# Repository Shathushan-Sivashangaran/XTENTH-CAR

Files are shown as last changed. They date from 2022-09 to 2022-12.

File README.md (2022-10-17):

# XTENTH-CAR
XTENTH-CAR (eXperimental one-TENTH scaled vehicle platform for Connected autonomy and All-terrain Research) aims to increase accessibility of experimental Connected Autonomous Vehicle (CAV) and Autonomous Ground Vehicle (AGV) research with low upfront costs, and complete Autonomous Vehicle (AV) hardware and software architectures, similar to the full-sized X-CAR experimental vehicle platform, enabling efficient cross-platform development between small-scale and full-scale vehicles [1], [2].

<p align="center">
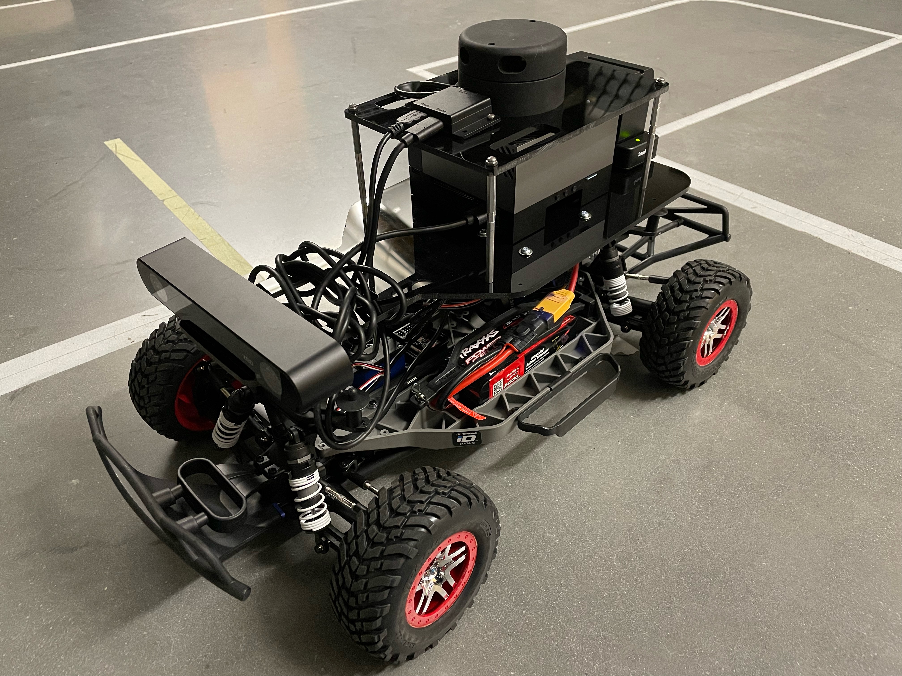
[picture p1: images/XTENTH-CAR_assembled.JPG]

</p>

## Hardware Build
The platform is equipped with the best-in-class NVIDIA Jetson AGX Orin System on Module (SOM), stereo camera with built-in Inertial Measurement Unit (IMU), barometer and magnetometer, 2D LiDAR and VESC, an open-source Electronic Speed Controller (ESC) with drivers written in the new Robot Operating System (ROS 2) to facilitate experimental CAV and AGV research that incorporate state-of-the-art computationally expensive algorithms such as Deep Reinforcement Learning. See [XTENTH-CAR/hardware](https://github.com/Shathushan-Sivashangaran/XTENTH-CAR/tree/main/hardware) for full Bill of Materials (BOM), CAD files and hardware assembly guide.

## Software Installation
NVIDIA Jetson series SOMs utilize the NVIDIA JetPack Software Development Kit (SDK) which includes bootloader, Linux kernel and Ubuntu desktop environment. XTENTH-CAR software is written using ROS 2 Foxy Fitzroy on JetPack v5+, which runs Ubuntu 20.04 natively.

1. See [NVIDIA JetPack SDK](https://docs.nvidia.com/jetson/jetpack/install-jetpack/index.html#package-management-tool) to install/upgrade JetPack components that include CUDA toolkit, cuDNN, TensorRT, OpenCV, NVIDIA container runtime with Docker integration, Multimedia API and NVSCI.

2. Install [ROS 2 Foxy Fitzroy](https://docs.ros.org/en/foxy/Installation/Ubuntu-Install-Debians.html), [colcon](https://docs.ros.org/en/foxy/Tutorials/Beginner-Client-Libraries/Colcon-Tutorial.html) and [rosdep](https://docs.ros.org/en/foxy/Tutorials/Intermediate/Rosdep.html) to build ROS 2 packages.

3. Clone the contents of [XTENTH-CAR/xtenthcar_ws/src](https://github.com/Shathushan-Sivashangaran/XTENTH-CAR/tree/main/xtenthcar_ws/src) into the src directory of a newly created ROS 2 workspace `xtenthcar_ws/src`.

4. See [XTENTH-CAR/xtenthcar_ws/README.md](https://github.com/Shathushan-Sivashangaran/XTENTH-CAR/blob/main/xtenthcar_ws/README.md) to install dependencies and create udev rules.

5. Build the workspace by running `colcon build` in the workspace root directory.

## Cite

For more information on XTENTH-CAR and full-size X-CAR refer to the following papers. Cite [1] if XTENTH-CAR was helpful to your research.

[1] S. Sivashangaran and A. Eskandarian, *“XTENTH-CAR: A Proportionally Scaled Experimental Vehicle Platform for Connected Autonomy and All-Terrain Research,”* arXiv preprint, 2022.

[2] G. Mehr, P. Ghorai, C. Zhang, A. Nayak, D. Patel, S. Sivashangaran, and A. Eskandarian, *“X-CAR: An Experimental Vehicle Platform for Connected Autonomy Research,”* IEEE Intelligent Transportation Systems Magazine, pp. 2–19, 2022.

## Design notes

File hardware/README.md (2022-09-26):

# Hardware Assembly

Acquire all the components in the Bill of Materials, and laser cut the acrylic sheet to fabricate mounting platforms for electronics using the provided [CAD files](https://github.com/Shathushan-Sivashangaran/XTENTH-CAR/tree/main/hardware/CAD_files). Use screws, nuts, washers, standoffs and velcro fasteners to complete the build.

1. Remove the stock Electronic Speed Controller (ESC), wireless receiver and antenna plastic housing from the chassis. Disconnect the DC brushless motor from the stock ESC, and steering servo motor from the wireless receiver.

2. Mount the VESC, ZED 2 stereo camera and SMALLRIG NP-F battery adapter plate to the laser cut base plate using screws, nuts and washers. Mount the USB 3.0 hub and NVIDIA Jetson Orin AGX Developer Kit using velcro fasteners. The VESC and USB 3.0 hub are mounted on the underside of the plate, and the other components are mounted on the top. Attach four 8" standoffs to the base plate to fasten to the roof plate.

3. Remove two screws each from the front and back of the chassis and replace with 6" standoffs. Screw the assembled base plate to the standoffs to mount it to the chassis.

4. Add bullet adapters to the DC brushless motor and connect it to the VESC. The white cable from the motor connects to cable A from the VESC, the yellow cable to B and blue cable to C.

5. Add 3 header pins to one end of the PPM extension cable and connect it to the steering servo motor. Connect the opposite end to the VESC PPM slot. Use a 1' micro USB cable to connect the VESC to the USB hub.

6. Mount the YDLIDAR G2 and data/power chip to the laser cut roof plate, and screw it to the standoffs attached to the base plate.

7. Connect the sensor USB cables to the USB hub.

8. Add the Traxxas 5000mAh 11.1V 3-cell LiPo battery to the chassis, and connect it to the VESC using the male TRX to female XT90 adapter.

9. Add the NP-F970 8800mAh battery to the SMALLRIG NP-F battery adapter plate, and connect it to the NVIDIA Jetson Orin AGX Developer Kit using a 5.5mm x 2.5mm 1' DC power cable.

10. Boot the Jetson Orin. Attach keyboard, mouse and monitor to install XTENTH-CAR software.

11. Remove the batteries when not in use.

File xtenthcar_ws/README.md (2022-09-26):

# ROS 2 Workspace

## Dependencies

Install ROS messages for vehicles using front-wheel Ackermann steering [ackermann_msgs](https://index.ros.org/r/ackermann_msgs/#foxy).

The YDLIDAR and ZED stereo camera ROS drivers require pre-installed SDKs. Install [YDLIDAR SDK](https://github.com/YDLIDAR/YDLidar-SDK) and [ZED SDK for Jetson](https://www.stereolabs.com/docs/installation/jetson/).

Add the following ROS 2 packages to the src directory of the workspace. 

1. [ROS 2 joystick driver](https://index.ros.org/p/joy/#foxy).
2. [ROS 2 YDLIDAR driver](https://github.com/YDLIDAR/ydlidar_ros2_driver).
3. [ROS 2 ZED driver](https://github.com/stereolabs/zed-ros2-wrapper).
4. [ROS 2 ZED examples for Rviz visualization](https://github.com/stereolabs/zed-ros2-examples).
5. [ROS 2 image_common package](https://github.com/ros-perception/image_common/tree/ros2).

The ZED driver requires image_common v3.0.0

```
cd image_common
git reset --hard a62ab876da2599627fe6a86bbc79040c62509422 # Reset to Release Tag: 3.0.0
```

## UDEV Rules

XTENTH-CAR requires knowledge of device names assigned by the operating system for VESC, YDLIDAR G2 and F710 Wireless Gamepad. These names can vary each time the Jetson SOM is rebooted. To assign stable device names, use the udev utility. 

1. Install the GNU nano text editor.

```
sudo apt update
sudo apt install nano
```

2. Assign VESC the name `/dev/sensors/vesc`.

```
sudo nano /etc/udev/rules.d/99-vesc.rules
```

Copy the VESC rule in a single line and save the file.

```
KERNEL=="ttyACM[0-9]*", ACTION=="add", ATTRS{idVendor}=="0483", ATTRS{idProduct}=="5740", MODE="0666", GROUP="dialout", SYMLINK+="sensors/vesc"
```

3. Assign YDLIDAR G2 the name `/dev/sensors/ydlidar`.

```
sudo nano /etc/udev/rules.d/99-ydlidar.rules
```

Copy the YDLIDAR G2 rule in a single line and save the file.

```
KERNEL=="ttyUSB[0-9]*", ACTION=="add", ATTRS{idVendor}=="10c4", ATTRS{idProduct}=="ea60", MODE="0666", GROUP="dialout", SYMLINK+="/sensors/ydlidar"
```

4. Assign F710 Wireless Gamepad the name `/dev/input/joypad-f710`.

```
sudo nano /etc/udev/rules.d/99-joypad-f710.rules
```

Copy the F710 Wireless Gamepad rule in a single line and save the file.

```
KERNEL=="js[0-9]*", ACTION=="add", ATTRS{idVendor}=="046d", ATTRS{idProduct}=="c21f", SYMLINK+="input/joypad-f710"
```

5. Activate the rules.

```
sudo udevadm control --reload-rules
sudo udevadm trigger
```

6. Reboot the system.

## Topics

`vesc/drive`: Publish `AckermannDriveStamped` messages to VESC.

`vesc/odom`: Pose and velocity data published by VESC.

`/scan`: Planer laser range data published by YDLIDAR G2.

`/zed2/zed_node/rgb/image_rect_color`: RGB color rectified image.

`/zed2/zed_node/point_cloud/cloud_registered`: Registered color point cloud.

`/zed2/zed_node/obj_det/objects`: Object detected frame by frame when the `enable_obj_det` service is called.

`/zed2/zed_node/imu/data`: Accelerometer, gyroscope, and orientation data in Earth frame.

`/zed2/zed_node/imu/mag`: Magnetometer data.

`/zed2/zed_node/atm_press`: Atmospheric pressure data.

`/zed2/zed_node/pose`: Absolute 3D position and orientation relative to the Map frame (Sensor Fusion algorithm + SLAM).

`/zed2/zed_node/path_map`: Sequence of camera poses in Map frame.

`/zed2/zed_node/path_odom`: Sequence of camera odometry poses in Map frame.

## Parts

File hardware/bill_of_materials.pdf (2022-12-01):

## XTENTH-CAR

## Bill of Materials

Item | Purchase Link
Traxxas Slash 4X4 VXL RC Car | https://traxxas.com/products/models/electric/slash-4x4-tsm?t=overview
Traxxas 5000mAh 11.1V 3-Cell LiPo Battery | https://traxxas.com/products/parts/batteries/idpowercellbatteries/lipo/2832X-5000mah-111v-3S-25C (https://traxxas.com/products/parts/batteries/idpowercellbatteries/lipo/2832X-5000mah-111v-3S-25C)
VESC 6 Mk VI Electronic Speed Controller | https://trampaboards.com/vesc-6-mkvi--copy-p-34848.html
150mm PPM Extension Cable | https://trampaboards.com/maytech-to-vesc-150mm-ppm-extension-cable--silicon-cable-24-awg-blackredwhite-p-24329.html (https://trampaboards.com/maytech-to-vesc-150mm-ppm-extension-cable--silicon-cable-24-awg-blackredwhite-p-24329.html)
Header Pins | https://www.amazon.com/DIKAVS-Break-Headers-Header-Connector/dp/B076F64ZCJ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 (https://www.amazon.com/DIKAVS-Break-Headers-Header-Connector/dp/B076F64ZCJ?link_code=qs)
Male TRX to Female XT90 Adapter | https://www.amazon.com/Padarsey-Traxxas-Female-Connector-Adapter/dp/B07QNB4TS2?th=1 (https://www.amazon.com/Padarsey-Traxxas-Female-Connector-Adapter/dp/B07QNB4TS2?th=1)
Bullet Adapter 4mm Male 3.5mm Female | https://www.amainhobbies.com/great-planes-bullet-adapter-4mm-male-3.5mm-female-3-gpmm3123/p608341 (https://www.amainhobbies.com/great-planes-bullet-adapter-4mm-male-3.5mm-female-3-gpmm3123/p608341)
1ft Micro USB Cable | https://www.amazon.com/dp/B095JZSHXQ/ref=sspa_dk_detail_1?psc=1&pd_rd_i=B095 JZSHXQ&pd_rd_w=b6vr2&content-id=amzn1.sym.3481f441-61ac-4028-9c1a- 7f9ce8ec50c5&pf_rd_p=3481f441-61ac-4028-9c1a- 7f9ce8ec50c5&pf_rd_r=GNA0GAJQGMHZT1629WGR&pd_rd_wg=2tzfQ&pd_rd_r=686ad 4ae-3216-44c5-b0af- 0e7f79124af4&s=pc&sp_csd=d2lkZ2V0TmFtZT1zcF9kZXRhaWxfdGhlbWF0aWM&spLa=Z W5jcnlwdGVkUXVhbGlmaWVyPUEzUDNKVURIRldCTE9JJmVuY3J5cHRlZElkPUEwODU3ND g4UzhWSTRVVFNPTEdFJmVuY3J5cHRlZEFkSWQ9QTA5MjUxODUxR1pZMDhQUVJMU1hC JndpZGdldE5hbWU9c3BfZGV0YWlsX3RoZW1hdGljJmFjdGlvbj1jbGlja1JlZGlyZWN0JmRvT m90TG9nQ2xpY2s9dHJ1ZQ (https://www.amazon.com/dp/B095JZSHXQ?s=pc&sp_csd=d2lkZ2V0TmFtZT1zcF9kZXRhaWxfdGhlbWF0aWM)
Logitech F710 Wireless Gamepad | https://www.amazon.com/Logitech-940-000117-Gamepad-F710/dp/B0041RR0TW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 (https://www.amazon.com/Logitech-940-000117-Gamepad-F710/dp/B0041RR0TW?hvadid=198084541101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)
NVIDIA Jetson AGX Orin Developer Kit | https://www.amazon.com/NVIDIA-Jetson-AGX-Orin-Developer/dp/B09WGRQP4B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 (https://www.amazon.com/NVIDIA-Jetson-AGX-Orin-Developer/dp/B09WGRQP4B?s=electronics)

WD_BLACK 1TB SN770 NVMe SSD | https://www.amazon.com/WD_BLACK-500GB-SN770-Internal-Gaming/dp/B09QV692XY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 (https://www.amazon.com/WD_BLACK-500GB-SN770-Internal-Gaming/dp/B09QV692XY)
NP-F970 8800mAh Battery | https://www.amazon.com/NP-F970-Battery-CCD-SC55-Handycams-Feelworld/dp/B08QTSMY3Q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 (https://www.amazon.com/NP-F970-Battery-CCD-SC55-Handycams-Feelworld/dp/B08QTSMY3Q)
SMALLRIG NP-F Battery Adapter Plate | https://www.amazon.com/SMALLRIG-Battery-Adapter-Plate-Material/dp/B092ZQDLRL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 (https://www.amazon.com/SMALLRIG-Battery-Adapter-Plate-Material/dp/B092ZQDLRL)
5.5mm x 2.5mm 1ft DC Power Cable Cord | https://www.amazon.com/Fancasee-Adapter-Surveillance-Security-Invoice/dp/B09TXN6SFG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 (https://www.amazon.com/Fancasee-Adapter-Surveillance-Security-Invoice/dp/B09TXN6SFG?s=electronics)
ZED 2 Stereo Camera | https://store.stereolabs.com/products/zed-2
YDLIDAR G2 | https://www.robotshop.com/en/ydlidar-g2-360-laser-scanner.html
7-Port USB 3.0 Hub | https://www.amazon.com/7-Port-Splitter-MacBook-Surface- iPhone/dp/B08GYQHPJQ/ref=sxin_16_ac_d_mf_br?ac_md=3-2-R1lPUkdLU0hJ- ac_d_mf_br_br&content-id=amzn1.sym.66ee1041-127b-4baf-8390- 1a597387172e%3Aamzn1.sym.66ee1041-127b-4baf-8390- 1a597387172e&crid=3AEXX8528OM87&cv_ct_cx=usb%2Bhub%2B7&keywords=usb%2B hub%2B7&pd_rd_i=B08GYQHPJQ&pd_rd_r=961c83b8-5dbe-4cfb-b3ab- eba161f70e4c&pd_rd_w=lv7DE&pd_rd_wg=WWBsE&pf_rd_p=66ee1041-127b-4baf- 8390- 1a597387172e&pf_rd_r=6MQQGSKZPTB4BF184C3Q&qid=1661021173&sprefix=usb%2B hubs%2B7%2Caps%2C1777&sr=1-3-4c1442dc-e644-4a05-a0d0-ff1b45d55b2f&th=1 (https://www.amazon.com/7-Port-Splitter-MacBook-Surface-iPhone/dp/B08GYQHPJQ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)
1/4" Acrylic Sheet for Laser Cut Platforms | https://www.amazon.com/Black-Acrylic-Plexiglass-Sheet- Thick/dp/B07KMQR4TP/ref=sr_1_8?crid=12R6TICILE4OI&keywords=1%2F4+acrylic+shee t+12x24&qid=1661136657&sprefix=1%2F4+acrylic+sheet%2Caps%2C52&sr=8-8 (https://www.amazon.com/Black-Acrylic-Plexiglass-Sheet-Thick/dp/B07KMQR4TP)

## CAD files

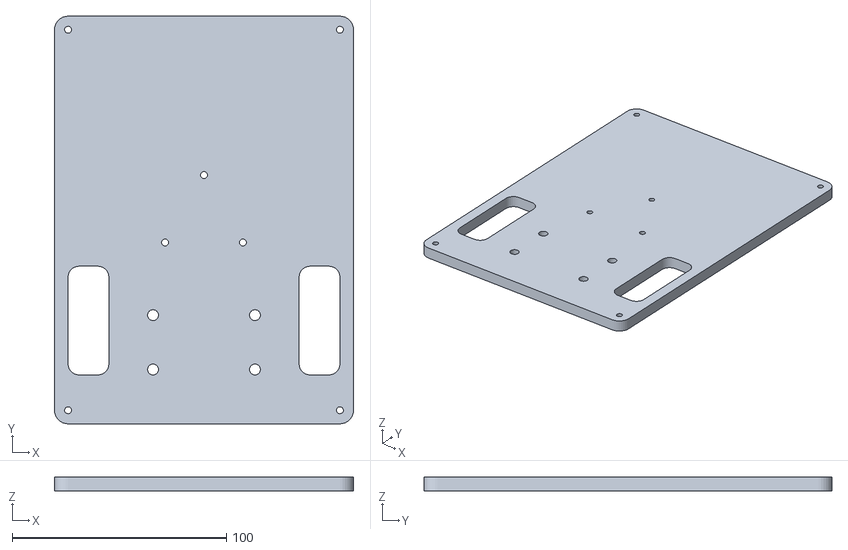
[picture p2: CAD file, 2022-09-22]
hardware/CAD_files/XTENTH-CAR_roofPlate.stl
139.7 x 190.5 x 6.35

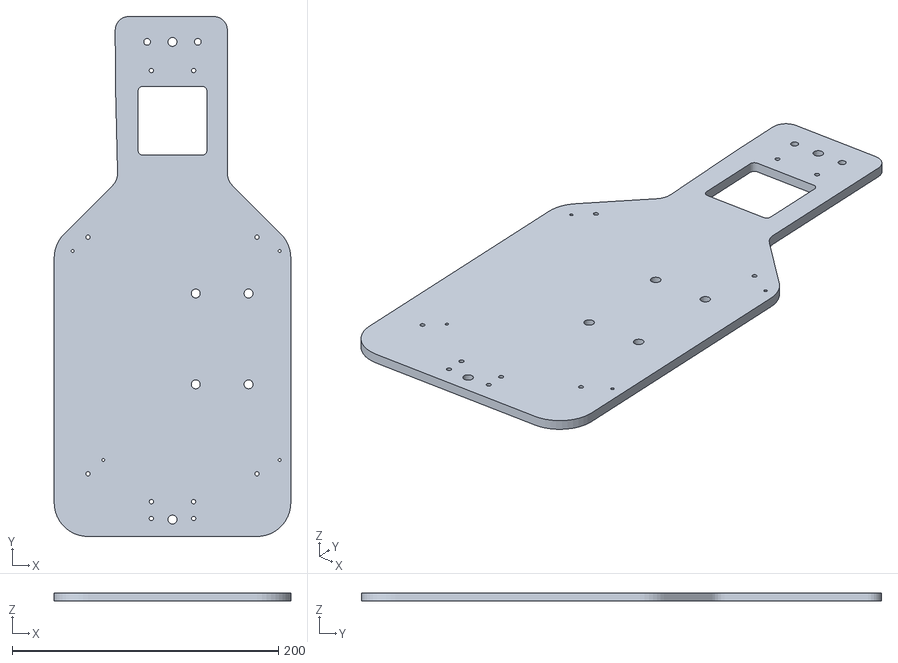
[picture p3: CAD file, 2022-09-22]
hardware/CAD_files/XTENTH-CAR_basePlate.stl
177.8 x 390.7 x 6.35

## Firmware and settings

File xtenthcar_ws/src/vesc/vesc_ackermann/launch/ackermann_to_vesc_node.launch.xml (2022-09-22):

<?xml version="1.0"?>
<launch>
  <!-- Optionally launch in GDB, for debugging -->
  <arg name="debug" default="false" />
  <let name="launch_prefix" value="xterm -e gdb --args" if="$(var debug)" />

  <!-- Ackermann to VESC node -->
  <node pkg="vesc_ackermann" exec="ackermann_to_vesc_node" name="ackermann_to_vesc_node" output="screen">
    <param name="speed_to_erpm_gain" value="4614.0" />
    <param name="speed_to_erpm_offset" value="0.0" />
    <param name="steering_angle_to_servo_gain" value="-1.2135" />
    <param name="steering_angle_to_servo_offset" value="0.5304" />
  </node>
</launch>

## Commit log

2022-09-20 Create BOM
2022-09-22 Create mount
2022-09-22 Create driver
